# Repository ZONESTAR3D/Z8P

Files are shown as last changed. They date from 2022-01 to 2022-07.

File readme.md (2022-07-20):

# Z8P Documents

### Download Z8P documents
[**Download all the Z8P documents in one go**](https://downgit.github.io/#/home?url=https:%2F%2Fgithub.com%2FZONESTAR3D%2FZ9%2Ftree%2Fmain%2FZ8P)     

## 1. Installation and User Guide
- [**Z8PM3(4) Installation and quick user guide V1.pdf**](./1.%20Installation%20and%20User%20Guide/Z8PM3(4)%20Installation%20and%20quick%20user%20guide%20V1.pdf)  Installation and quick user guide.    
- [**Z8PM3(4)-Pro Installation and quick user guide V1.pdf**](./1.%20Installation%20and%20User%20Guide/Z8PM3(4)Pro%20Installation%20and%20quick%20user%20guide%20V1.pdf)  Installation and quick user guide.  
- [**LCD2864 Menu Description.pdf**](./1.%20Installation%20and%20User%20Guide/LCD12864%20Menu%20Description%20V6.pdf)  for Z8PM3(4), 128x64 LCD screen Menu instruction
- [**LCD-DWIN Menu Description.pdf**](./1.%20Installation%20and%20User%20Guide/LCD-DWIN%20MENU%20Description%20V1_2.pdf) for Z8PM3(4)Pro, 4.3" TFT-LCD screen MENU instruction of 
- [**Z8PM3(M4) Wiring Diagram.jpg**](./1.%20Installation%20and%20User%20Guide/Z8P_Wirig%20Diagram.jpg)  Wiring Diagram for Z8PM3(4)
- [**Z8PM3(M4)-Pro Wiring Diagram.jpg**](./1.%20Installation%20and%20User%20Guide/Z8P_Pro_Wirig%20Diagram.jpg)  Wiring Diagram for Z8PM3(4)-Pro  
- [**How to Load and Unload filament.pdf**](./1.%20Installation%20and%20User%20Guide/How%20to%20Load%20and%20Unload%20filament%20(LCD12864).pdf) Instrution for how to load and unload filament.  
- [**Operature guide for Mixing Color Printer.pdf**](./1.%20Installation%20and%20User%20Guide/Operature%20guide%20for%20Mixing%20Color%20Printer%20V1_2.pdf) Instrution for Operate the Mixing Color Extruder. 
- [**Bed auto leveling**](./1.%20Installation%20and%20User%20Guide/Bed%20Auto%20Leveling/) This directory has instructions on how to do the auto leveling and a leveling test gcode file. 
- [**Advanced Features**](./1.%20Installation%20and%20User%20Guide/Advanced%20Features/) Instrution for Advanced Features.  
## 2.Slicing
Please click this link to read the newest [**slicing guide**](https://github.com/ZONESTAR3D/Slicing-Guide).  
## 3. Test gcode
[Included some gcode files for testing.](./3.%20Test%20gcode/)
## 4. FAQ
[Included some TroubleShootings files.](./4.%20FAQ/)
## 5. Firmware   
- [**Firmware hex file**](https://github.com/ZONESTAR3D/Firmware/tree/master/Z8/Z8P)   
- [**Firmware sourc code**](https://github.com/ZONESTAR3D/source-code-for-3d-printer)
## 6. Video tutorial
### :movie_camera:[Installation Guide](https://youtu.be/YV3dSoo5NOM)  
### :movie_camera:[Product introduction](https://youtu.be/NqhwHJeaFhI)

## 7. Parts STL
Inlcuded the print parts stl fils for Z8P.

## How to downlod files from Github page
#### Step 1: Click this link [**https://downgit.github.io/**](https://downgit.github.io/) 
#### Step 2: Copy the Github file or direcotry link which you want to download.
#### Step 3: Click download button and wait a few seconds, it will start to download automatically. 
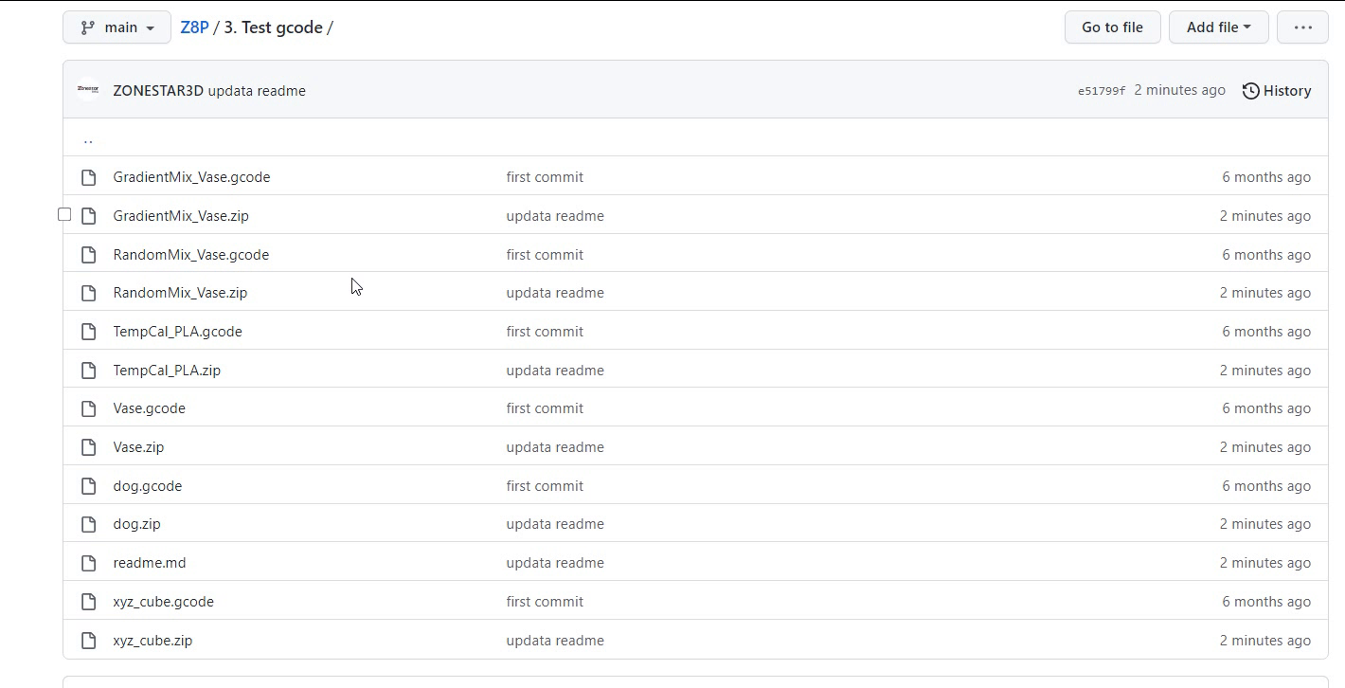
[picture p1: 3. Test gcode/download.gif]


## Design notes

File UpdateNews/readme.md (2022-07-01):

## Summary of Updates for ZONESTAR Z8P
### Updates in 2022-04-25
1. Release firmware V2.0.0 [View](https://github.com/ZONESTAR3D/Firmware/tree/master/Z8/Z8P/ZM3E4/released)
2. **E4 HOTEND** Update E4 hotend slicing settings [View](https://github.com/ZONESTAR3D/Upgrade-kit-guide/tree/main/HOTEND/E4%204-IN-1-OUT%20Non-Mixing%20Color%20Hotend/example)
3. **Slicer** Update PrusaSlcier prifiles for Z8(Z9)+E4 hotend and [View](https://github.com/ZONESTAR3D/Slicing-Guide/tree/master/PrusaSlicer)

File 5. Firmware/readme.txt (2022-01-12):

Firmware Upload Steps:
====
1. Download the zip file and unzip it
2. Copy firmware.bin to the root directory of Micro-SD card
3. Power off the printer and plug the Micro-SD card into socket on control board
4. Power on the printer, push the power button and wait about 30 seconds
5. Do the below step on LCD screen to initialize EEPROM after upload firmware:
MENU>>config>>Restore Defaults

Firmware
====
[**Firmware download link:**](https://github.com/ZONESTAR3D/Firmware/tree/master/Z8/Z8P)
[**Firmware Source code download link:**](https://github.com/ZONESTAR3D/source-code-for-3d-printer)

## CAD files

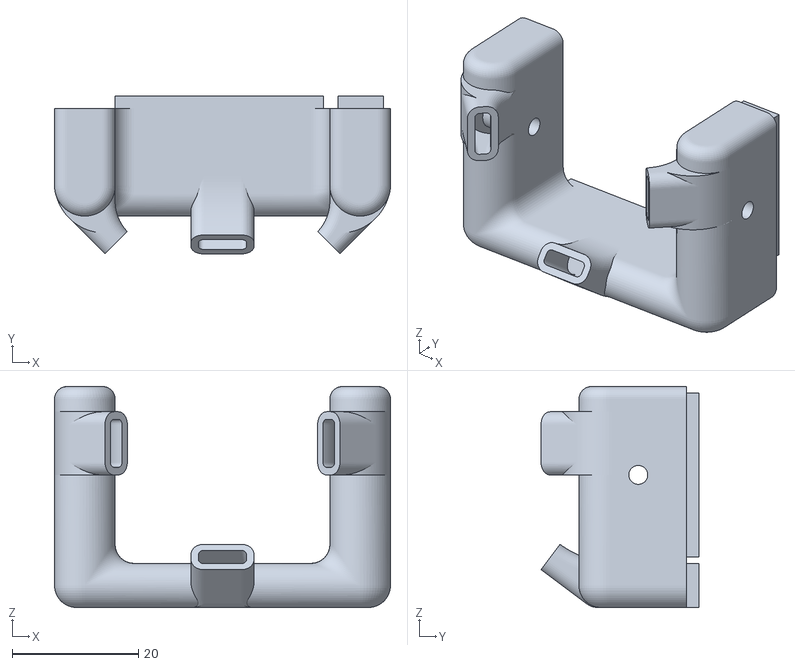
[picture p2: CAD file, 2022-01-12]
4. FAQ/fan_duck_m4_v3.stl
53.2 x 25.0 x 35.0

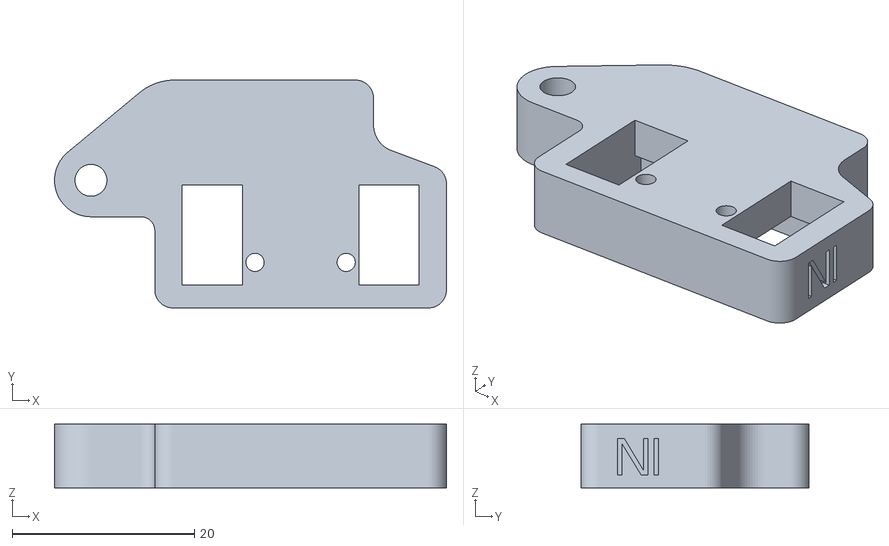
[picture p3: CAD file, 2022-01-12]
7. Parts STL/FRODV6-B.stl
43.0 x 25.0 x 7.00

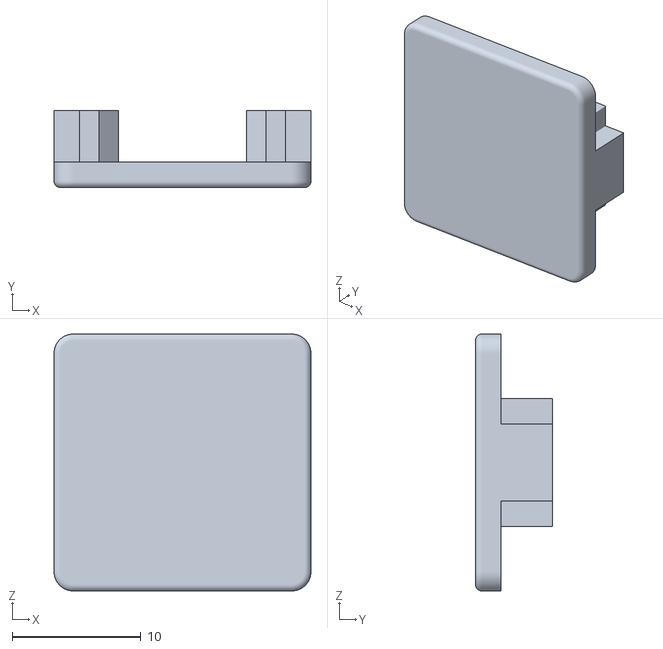
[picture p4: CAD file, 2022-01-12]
7. Parts STL/cap_af_20v.stl
20.0 x 6.00 x 20.0

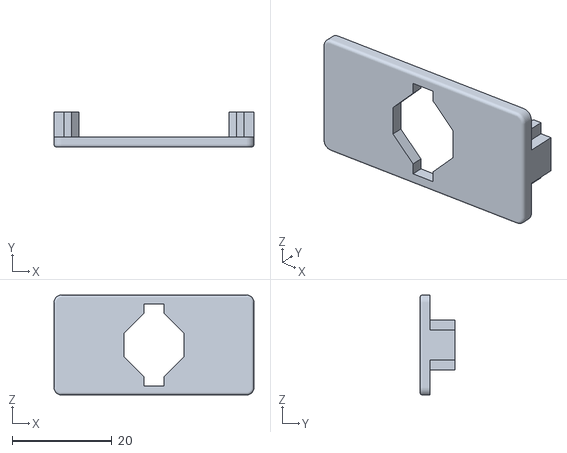
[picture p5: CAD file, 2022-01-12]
7. Parts STL/cap_af_40v.stl
40.0 x 7.00 x 20.0

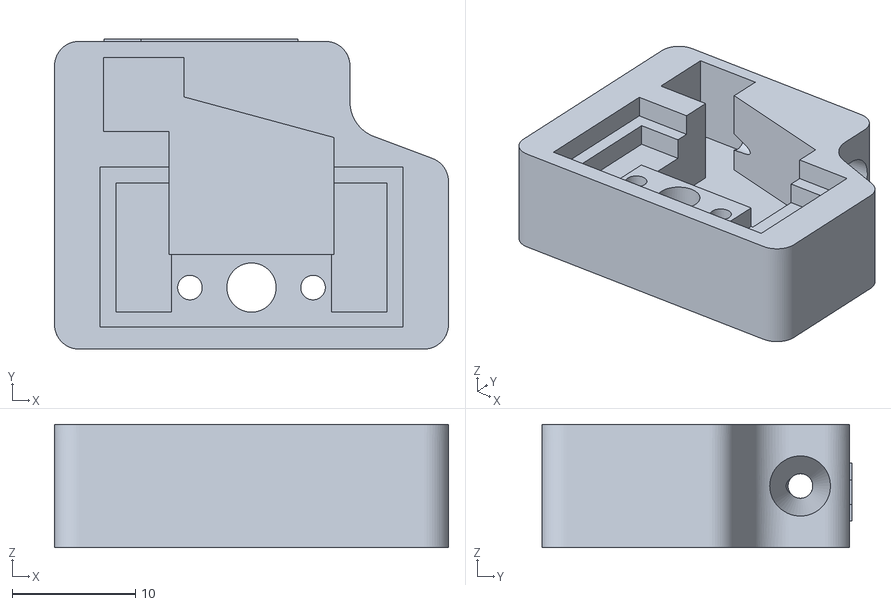
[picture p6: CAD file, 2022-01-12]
7. Parts STL/FRODV6-A.stl
32.0 x 25.2 x 10.0

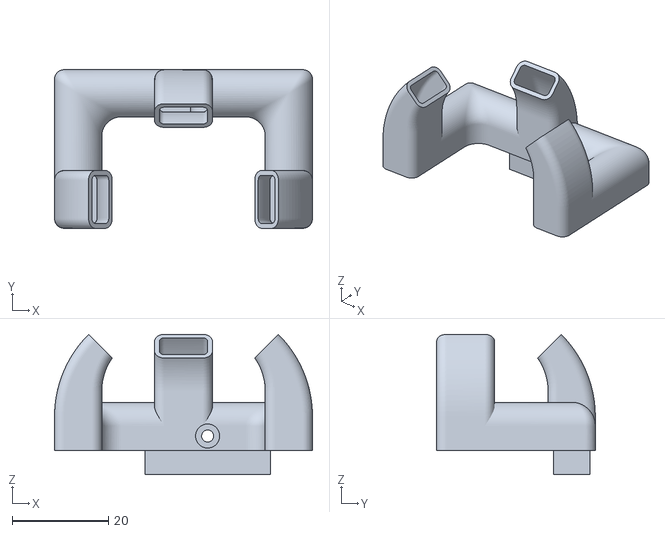
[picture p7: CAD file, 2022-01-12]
7. Parts STL/fanduck_m3_v4.stl
53.5 x 32.9 x 29.1

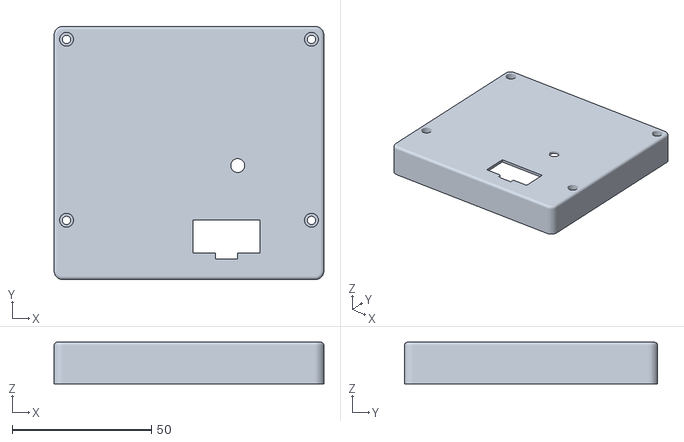
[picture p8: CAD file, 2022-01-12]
7. Parts STL/lcd12864_case_v2.stl
97.0 x 91.0 x 15.0

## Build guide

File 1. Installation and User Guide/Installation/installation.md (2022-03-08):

# Z8P Installation Guide
### :bangbang: ATTENTION :bangbang:
+ :warning: Please strictly follow the standard operation when installation.
+ :warning: Please put the printer away from the reach of kids.
+ :warning: Must be guided by adults when children are installed or used.
+ :zap: Take care when installation, to avoid electrical shock hazards.
+ :hotsprings: Hotend has high temperature even the printer stop working.
+ :hotsprings: Hotbed has high temperature even the printer stop working.
+ :dash: Keep well-ventilated condition! May produce toxic gases when printing.
+ :warning: Make sure the AC power select switch set correctly before power on.

## 1. Parts
### Parts list
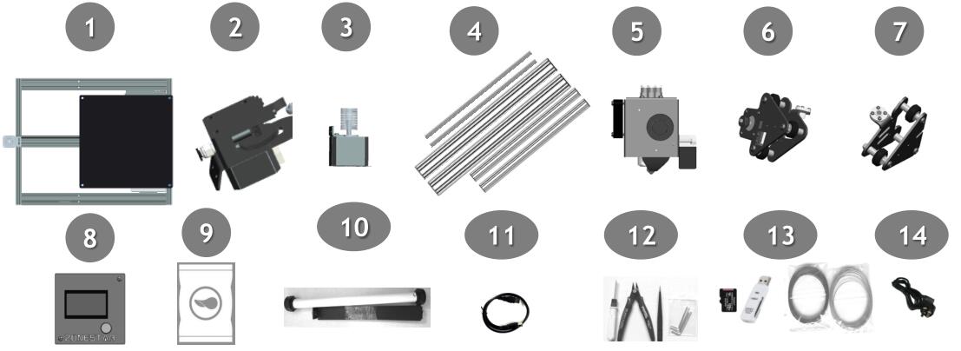
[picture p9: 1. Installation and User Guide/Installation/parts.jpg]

>
1. Base Module.    
2. Extruders Module (3 sets for M3 and 4 sets for M4).    
3. 2x Z-axis Motor Modules.  
4. Lead screw & Profiles.  
5. Print head with bracket (M3 or M4 hotend assembly).
6. Z carrier left.
7. Z carrier right.
8. Contol Panel (128x64 for Z8PM3(4) and TFT-LCD for Z8PM3(4)-Pro).  
9. Accessories bag, include: Scews, lead screws fix blocks, ENDSTOPs, Fittings,
PTFE Tubes, belt, cable tie, etc.  
10. Filament roll bracket.  
11. USB cable.  
12. Tools.  
13. SD card, Card Reader, Gift filament.  
14. AC power cord.  

### Parts description
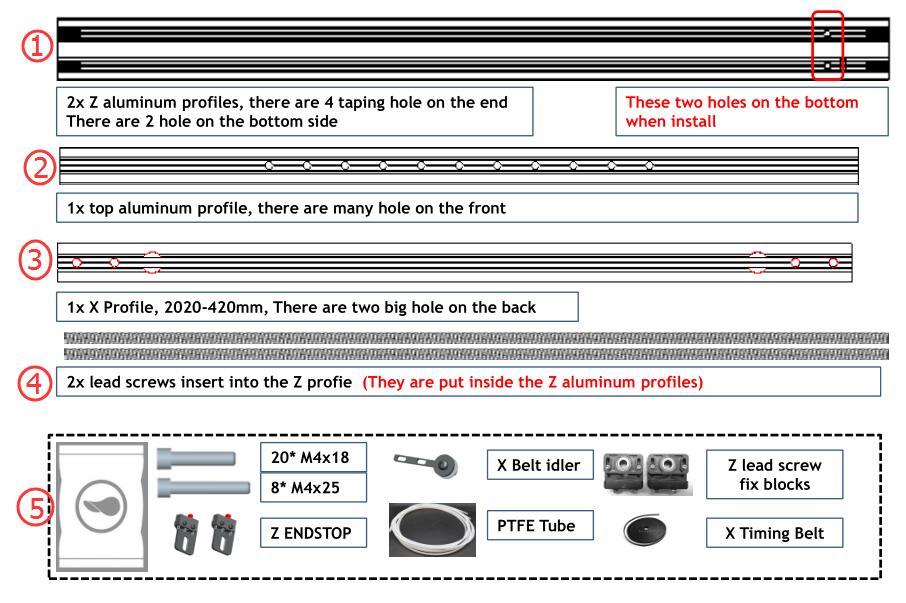
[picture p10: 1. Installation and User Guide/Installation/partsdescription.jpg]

>
1. Please note when install Z-profiles that side with two holes should be at the bottom.  
2. Pay attention to distinguish between X profile and TOP profile. The one with many holes is the TOP profile.  
3. Pay attention to the installation direction of the X profile. The side with two large holes faces back (touched the sheet metal of the Z carriers).  
4. The z-axis lead screw are placed in the z-axis profiles.  
5. Please check the packaging in the accessories bag.    

## 2. Installation
### 2-1: Install Z axis parts
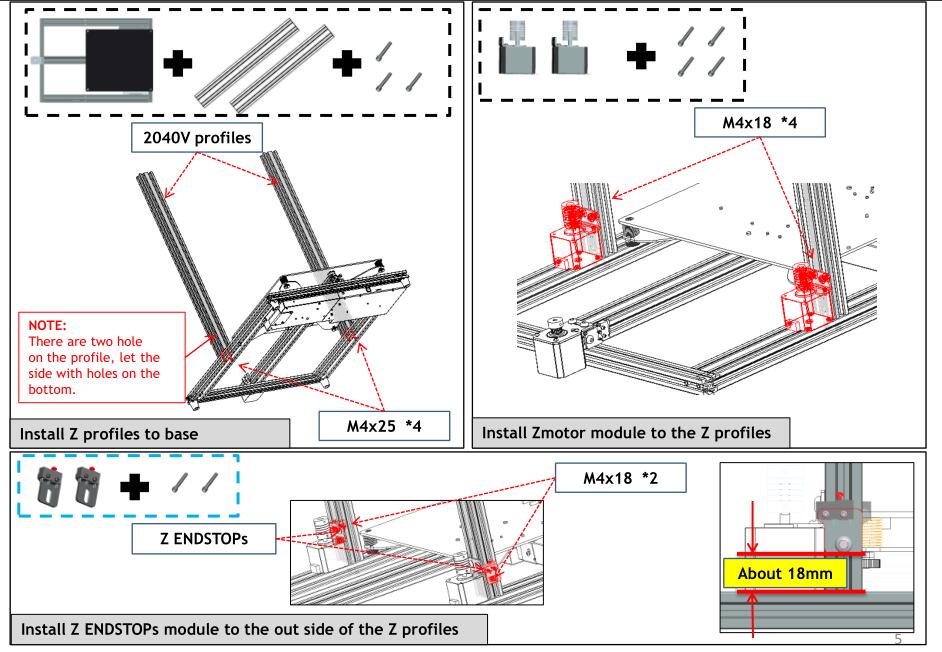
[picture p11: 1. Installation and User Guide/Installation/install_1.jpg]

> 
1. The side with 2 holes of the Z profiles is downward.
2. Alignment the side  of Z axis profile and the side of bottom profile of base module.  
3. Before installing the z-axis motor module on the profile, loosen the two screws fixing the motor a little.  
4. The Z ENDSTOPs should be mounted on the outside, and the install heigth is about about 18mm.

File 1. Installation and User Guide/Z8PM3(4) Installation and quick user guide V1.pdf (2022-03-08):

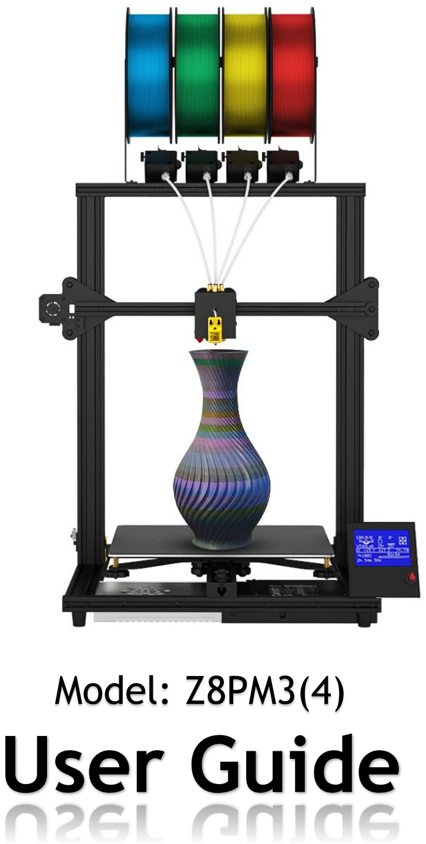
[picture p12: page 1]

# Model: Z8PM3(4)

# User Guide

Please put the printer away from the reach of kids.

Must be guided by adults when children are installed or used.

Take care when installation, to avoid electrical shock hazards.

## Please keep well-ventilated condition! May produce toxic gases when

printer working.

## Caution: Hot!

Hotend has high temperature even the printer stop working.

## Caution: Hot!

Hotbed has high temperature even the printer stop working.

Please strictly follow the standard operation when installation.

## Please make sure you have set the AC power select switch to the

correct position before power on.

## The newest documents download link:

## https://github.com/ZONESTAR3D/Z8P

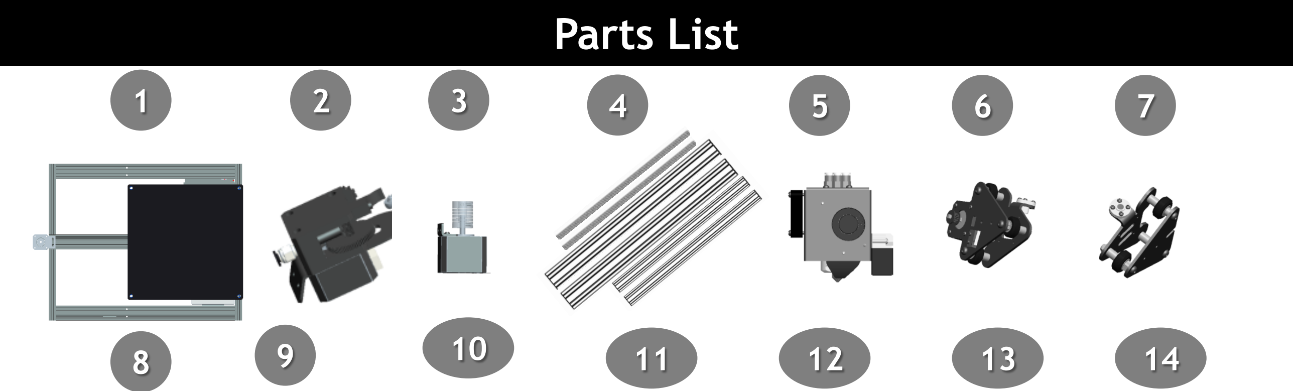
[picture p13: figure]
Parts List

No. | Name | Check | No. | Name | Check
1 | Base Module | □ | 8 | Contol Panel | □
2 | Extruders (3 sets for M3 and 4 sets for M4) | □ | 9 | Scews, lead screws fix blocks, ENDSTOPs, Fittings, PTFE Tubes, belt, cable tie, etc. | □
3 | Z-axis Motor Modules (2 sets) | □ | 10 | Filament Roll Bracket | □
4 | Lead screw & Profiles | □ | 11 | USB cable | □
5 | Print head with bracket M3 or M4 hotend | □ | 12 | Tools | □
6 | Z carrier left | □ | 13 | SD card, Card Reader, Gift filament | □
7 | Z carrier right | □ | 14 | Power cord | □

# Parts

2x Z aluminum profiles, there are 4 taping hole on the end There are 2 hole on the bottom side

These two holes on the bottom when install

1x top aluminum profile, there are many hole on the front

1x X Profile, 2020-420mm, There are two big hole on the back

2x lead screws insert into the Z profie (They are put inside the Z aluminum profiles)

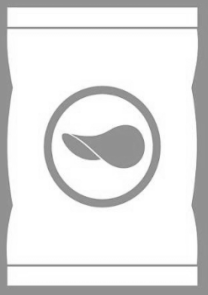
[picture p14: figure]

20* M4x18

8* M4x25

Z ENDSTOP

X Belt idler

PTFE Tube | X Timing Belt Z lead screw fix blocks

# Install Z axis Parts

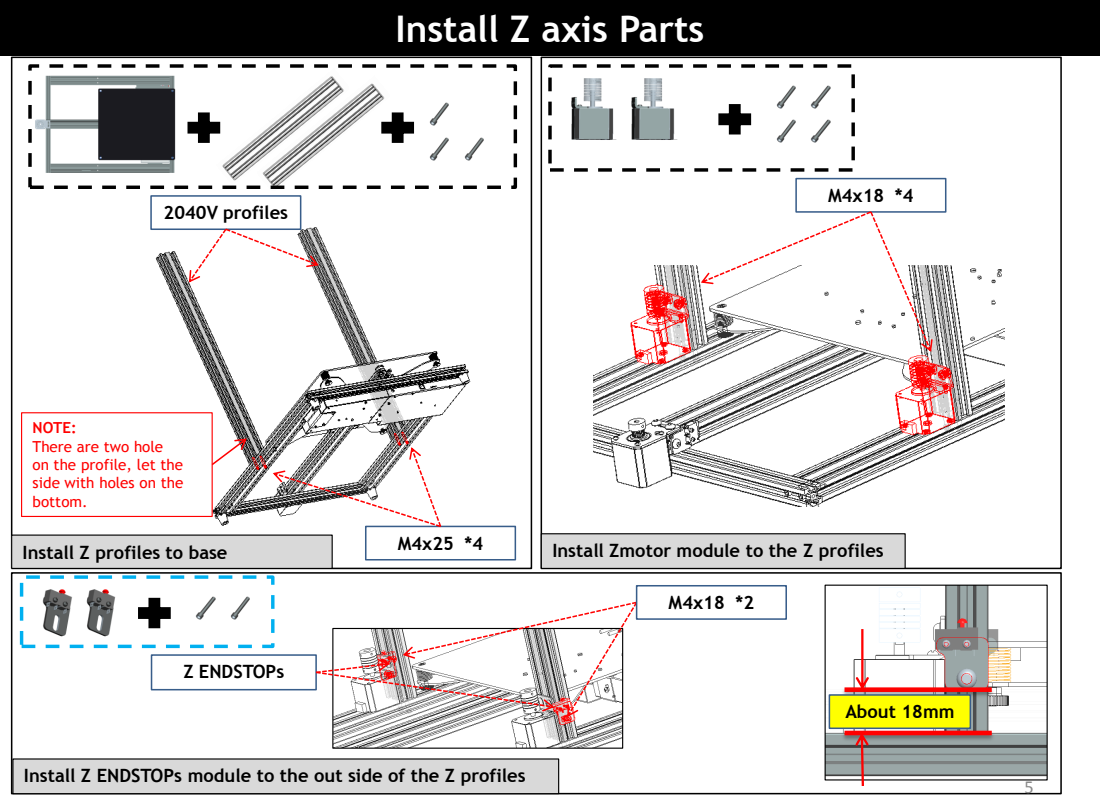
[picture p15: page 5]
2040V profiles; Z ENDSTOPs; About 18mm

NOTE:
There are two hole
on the profile, let the
side with holes on the
bottom.

Install Zmotor module to the Z profiles

Install Z profiles to base

Install Z ENDSTOPs module to the out side of the Z profiles

# Install Z axis Parts

Install Z Carrier | Install lead screws

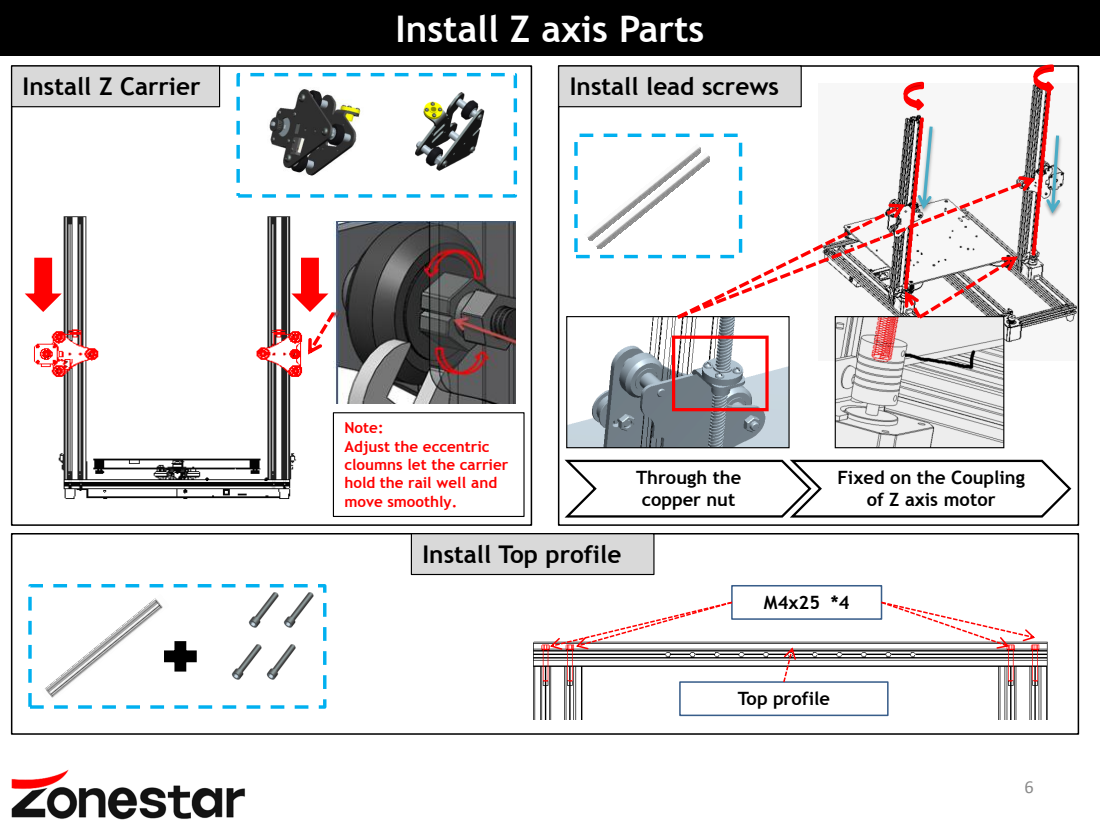
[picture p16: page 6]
Through the copper nut; Top profile

Note:
Adjust the eccentric
cloumns let the carrier
hold the rail well and
move smoothly.

Fixed on the Coupling
of Z axis motor

Install Top profile

# Install X axis Parts

## Install X belt idler and X profile

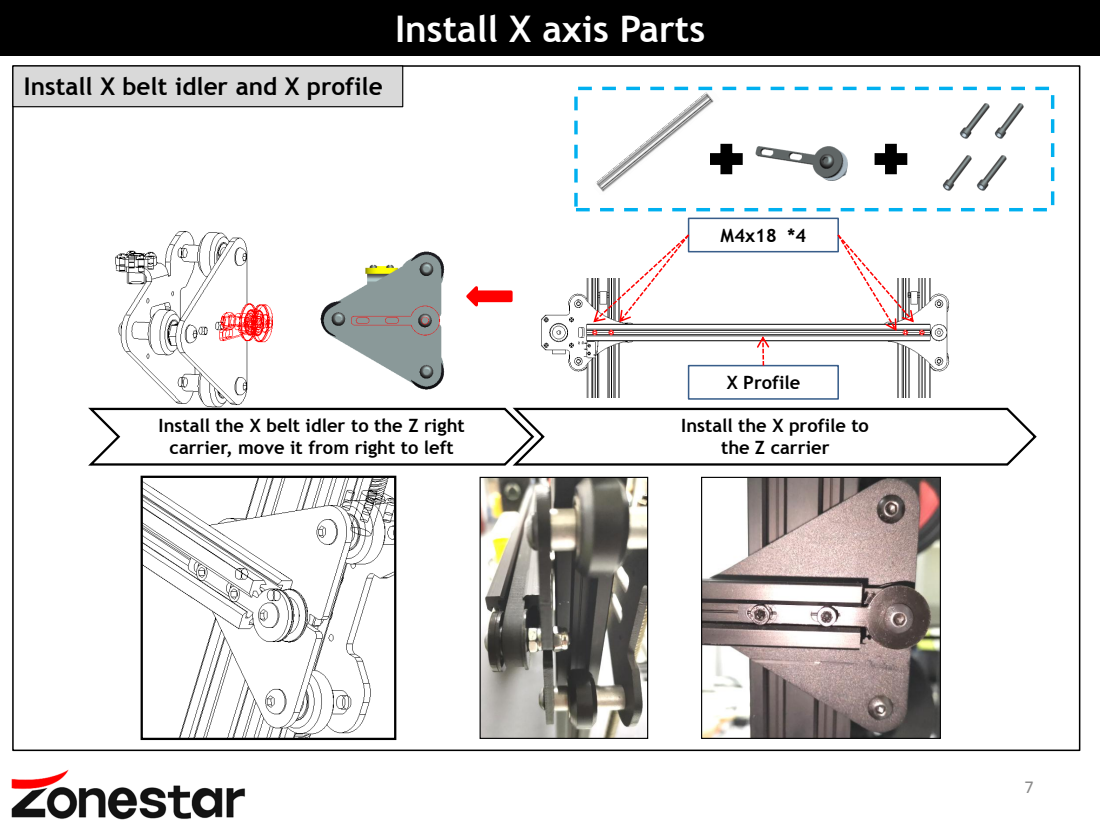
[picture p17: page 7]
X Profile

Install the X belt idler to the Z right
carrier, move it from right to left

Install the X profile to
the Z carrier

# Install X axis Parts

## Install X profile

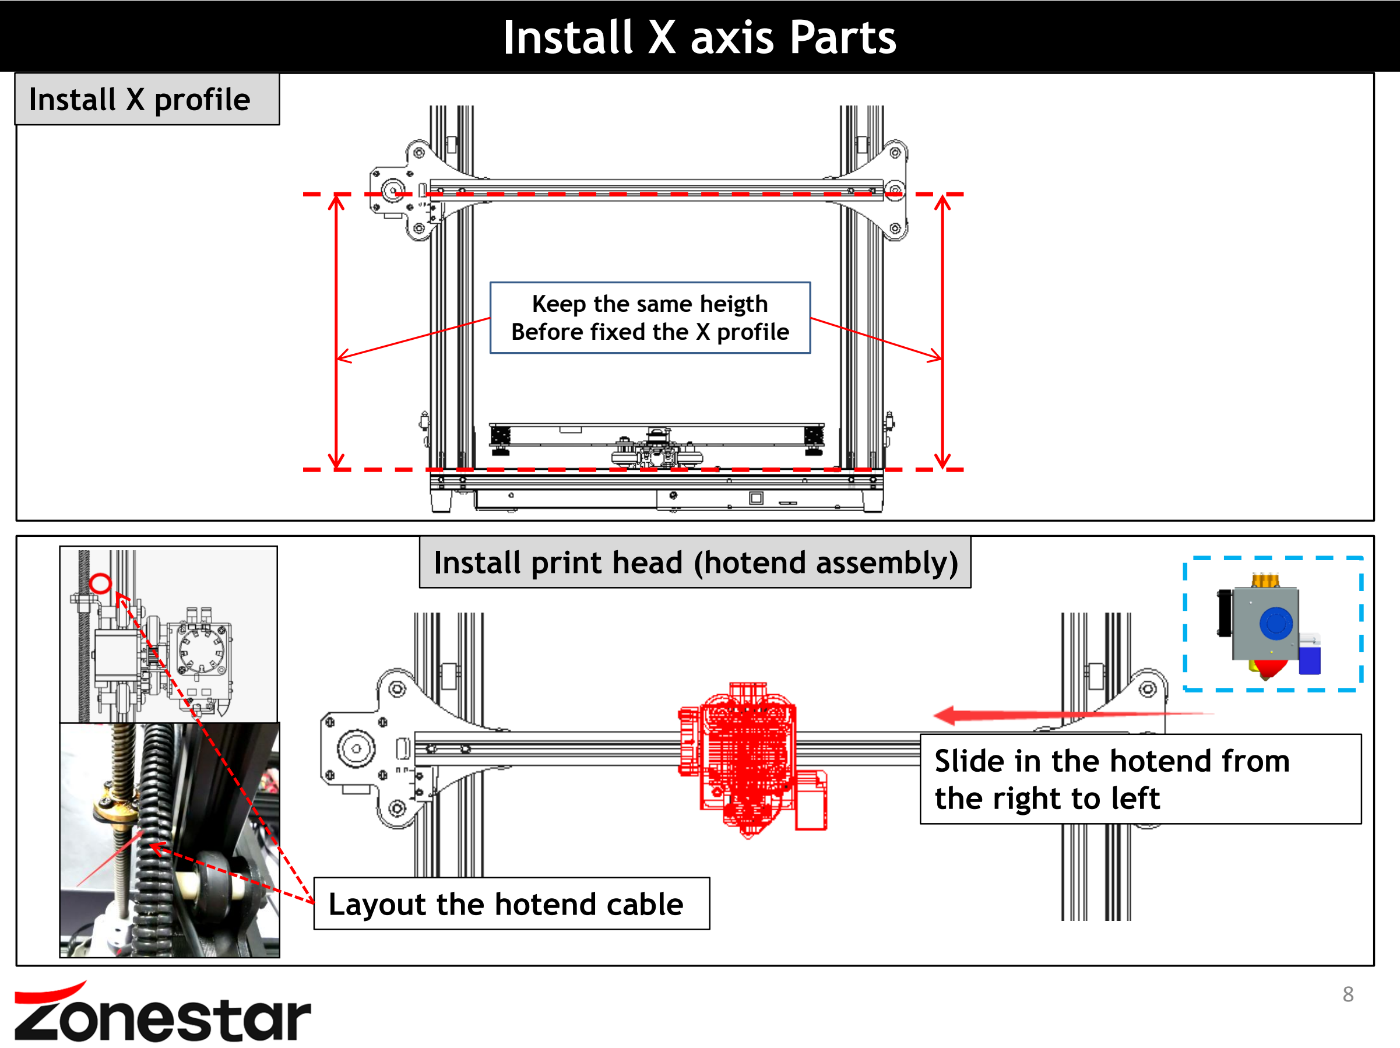
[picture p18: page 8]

## Slide in the hotend from the right to left

## Layout the hotend cable

Keep the same heigth
Before fixed the X profile

## Install print head (hotend assembly)

# Install X belt

## Install the X belt

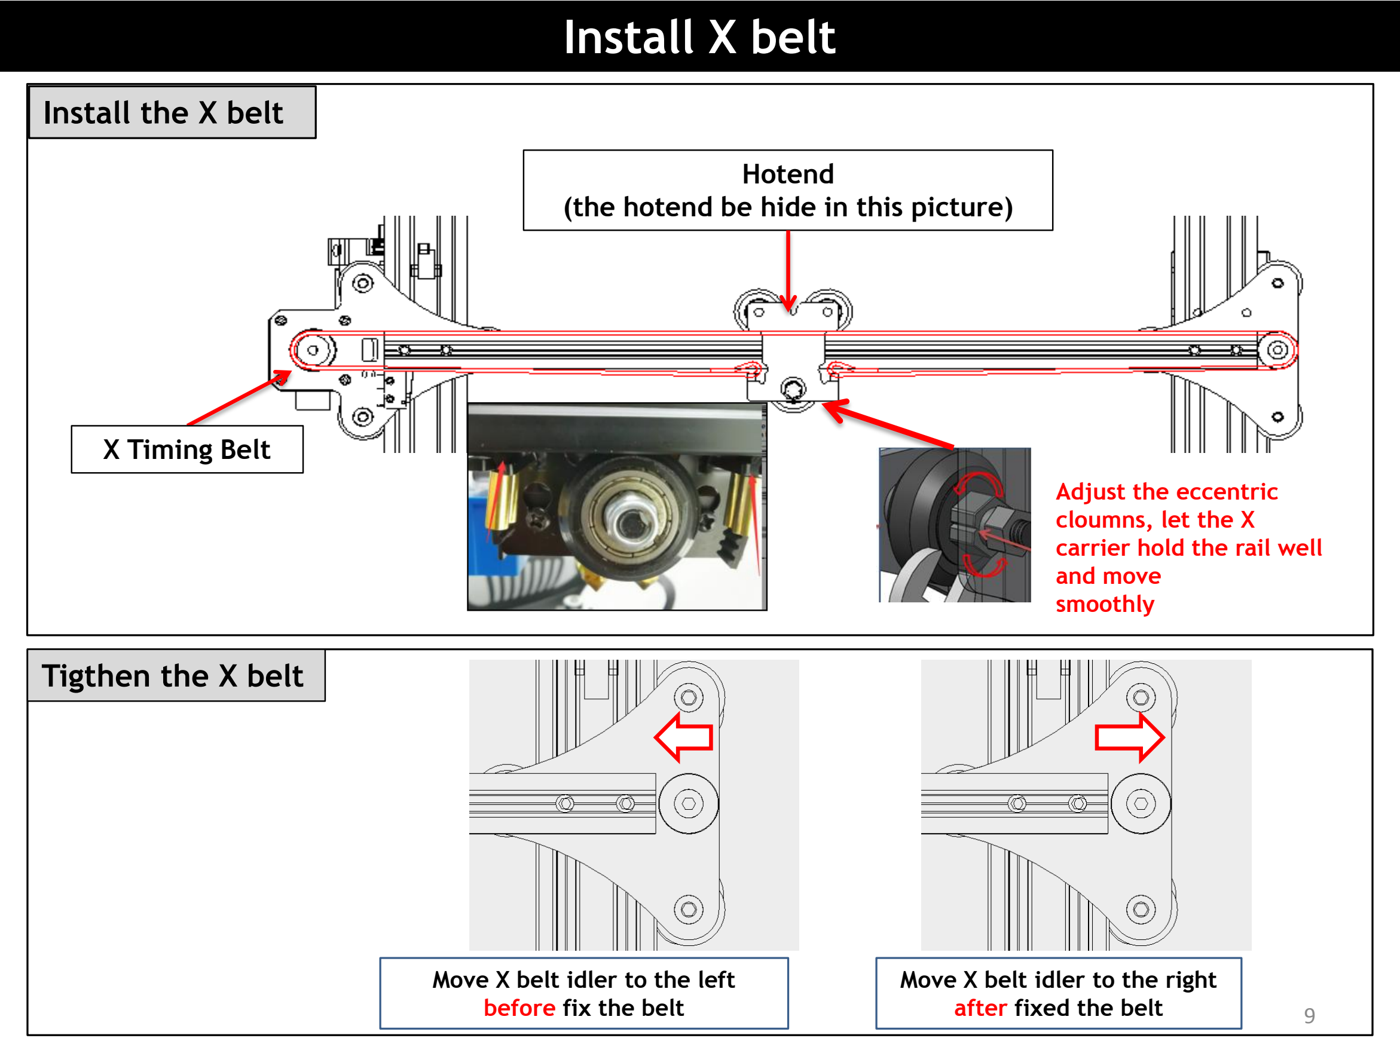
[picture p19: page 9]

Move X belt idler to the right
after fixed the belt | 9

Move X belt idler to the left before fix the belt

## Tigthen the X belt

X Timing Belt

Hotend
(the hotend be hide in this picture)

Adjust the eccentric
cloumns, let the X
carrier hold the rail well and move
smoothly

# Install the other parts

## x 3 o r 4

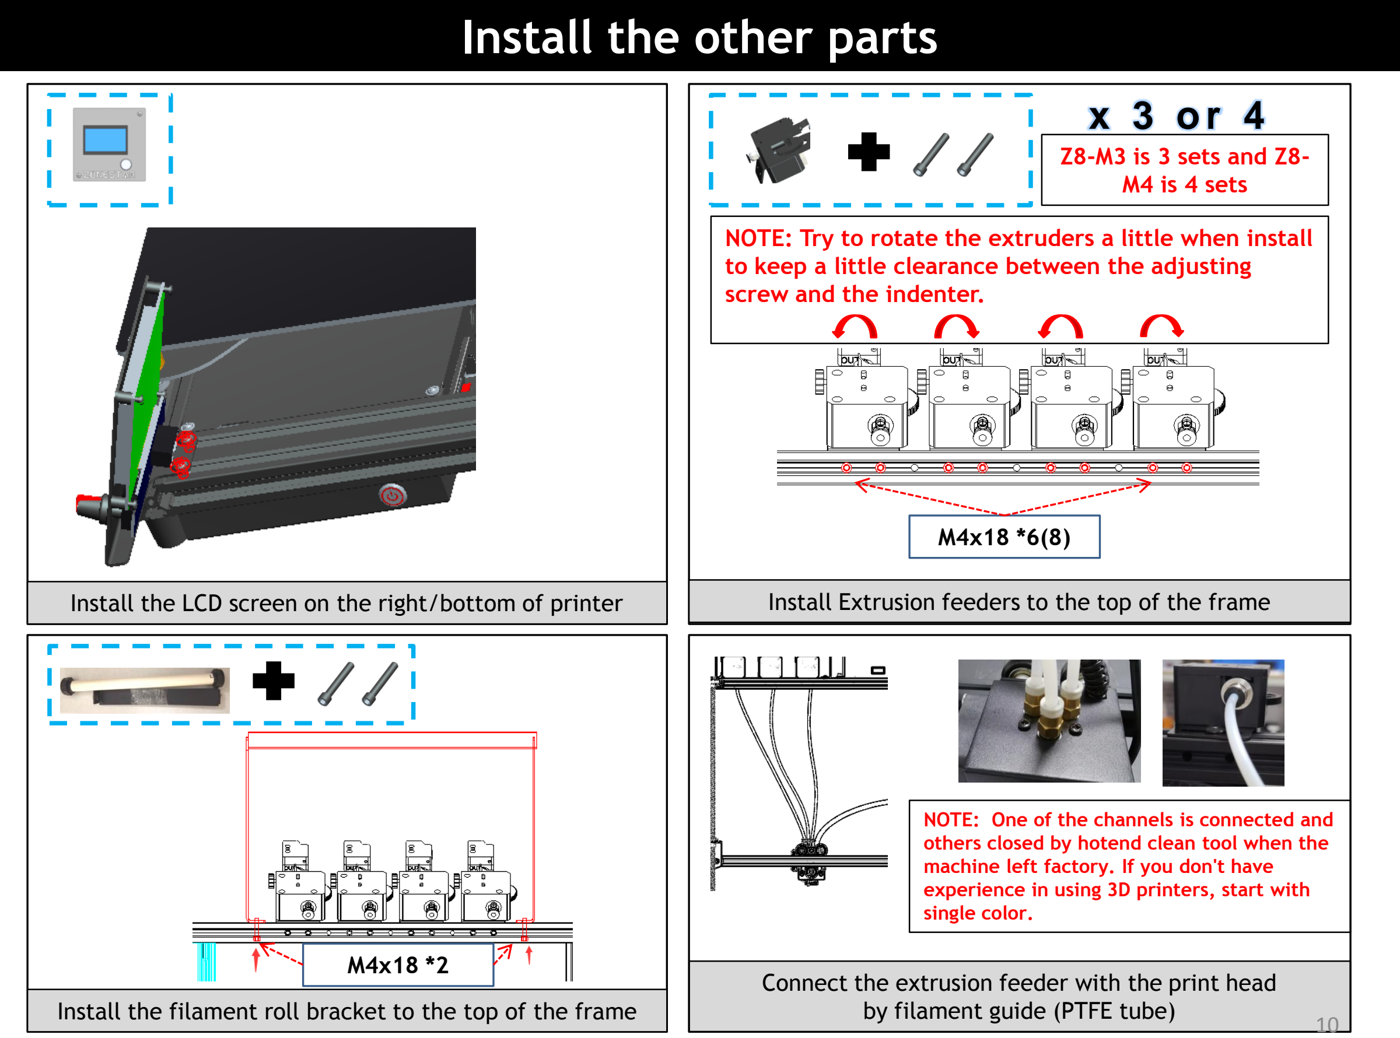
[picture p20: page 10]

Install the LCD screen on the right/bottom of printer

Z8-M3 is 3 sets and Z8-
M4 is 4 sets

Install the filament roll bracket to the top of the frame

Connect the extrusion feeder with the print head by filament guide (PTFE tube)

NOTE: One of the channels is connected and others closed by hotend clean tool when the machine left factory. If you don't have experience in using 3D printers, start with single color.

Install Extrusion feeders to the top of the frame

M4x18 *6(8)

NOTE: Try to rotate the extruders a little when install to keep a little clearance between the adjusting screw and the indenter.

M4x18 *2

Keep the lead screws parallel to the Z axis profiles as far as possible will help to obtain better printing quality, please debug them refer to the following steps: Step 1. Loosen all the screws a little that fixed the Z motors and T8 copper nut. Step 2. Synchronous Rotate the couplings to move up the X axis to 1/2 height of the printer. Step 3. Keep the lead screws parallel to the Z profiles, then tighten the screws that fixed the Z motor

| Loosen a little

and T8 copper nuts.
Step 4. Install the Z lead screws fix blocks on the top profile after done.

200mm

Put in

Fixed

Fixed

# Adjust height of Z ENDSTOPs

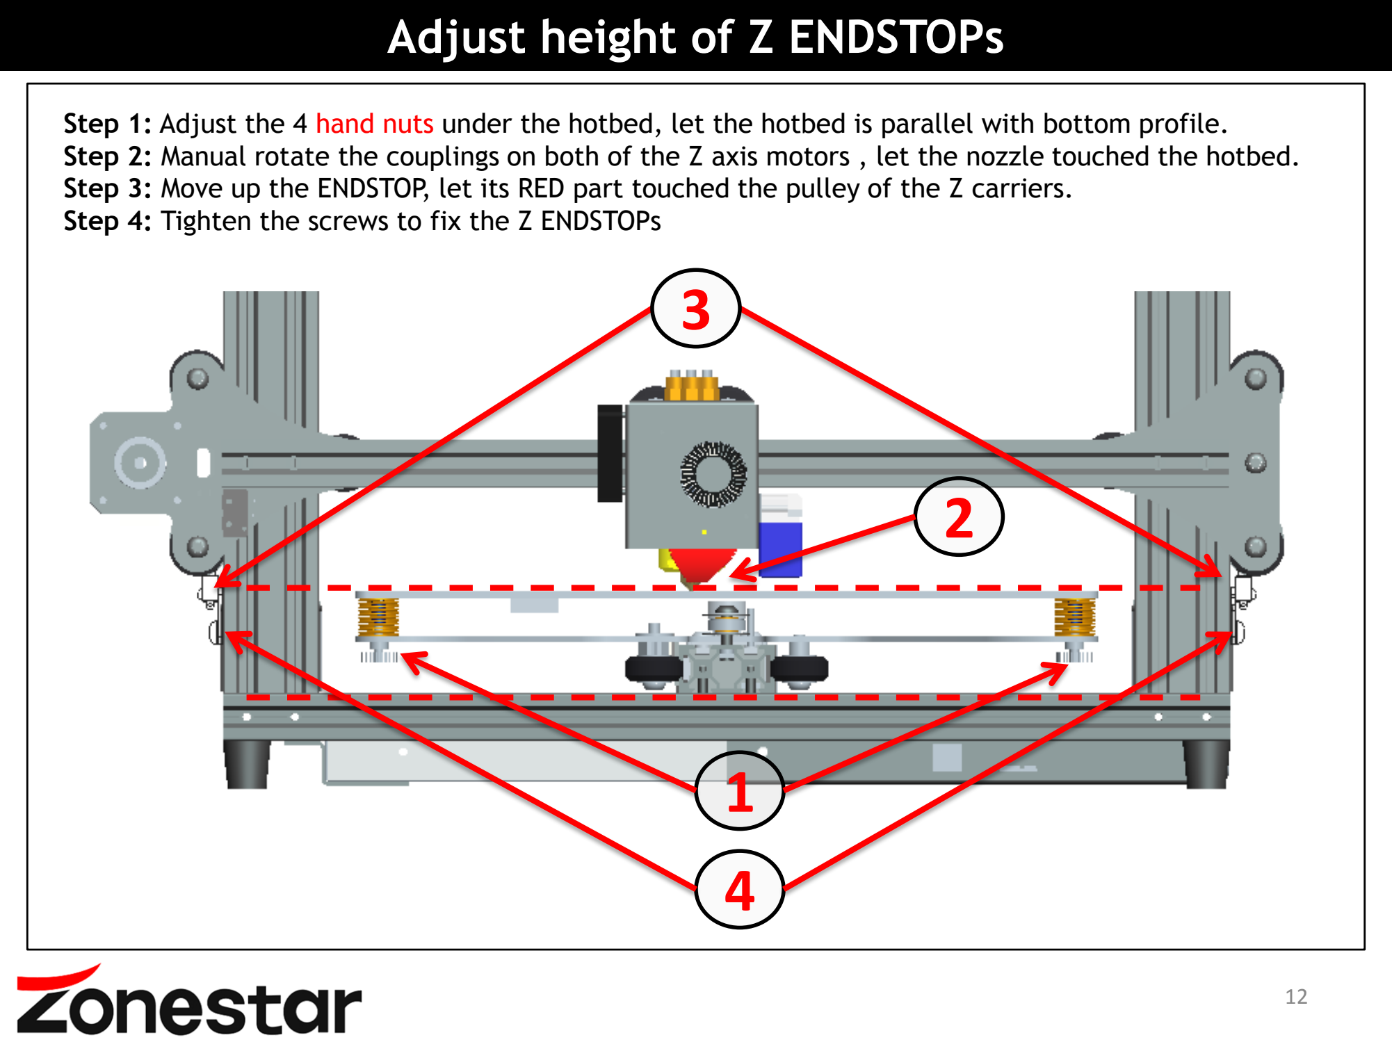
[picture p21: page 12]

Step 1: Adjust the 4 hand nuts under the hotbed, let the hotbed is parallel with bottom profile.
Step 2: Manual rotate the couplings on both of the Z axis motors , let the nozzle touched the hotbed.
Step 3: Move up the ENDSTOP, let its RED part touched the pulley of the Z carriers.
Step 4: Tighten the screws to fix the Z ENDSTOPs

1

2

4

3

## Take care when installation, to avoid electrical shock hazards!

## Double check the wiring! WRONG WIRING MAY DAMAGED THE ELECTRONIC DEVICE!

## Set the 110V/220V swicth (on the side of power supply) to correct position according to your city power voltage!

## Put the motor wire to the grooves of profile and cover them by

plastic profile cover, and using cable tie to wrap the free wires.

## Stop working immediately if the motor has abnormal vibration or noise,, otherwise the driver modules may be damaged!

## Make sure the hotend cooling fan is working when the nozzle

temperature is over 60 degree, otherwise check the wiring again.

## DC-IN, HOTBED has lager operating current, please make sure

these wires contact well with the terminal.

# About electronics parts

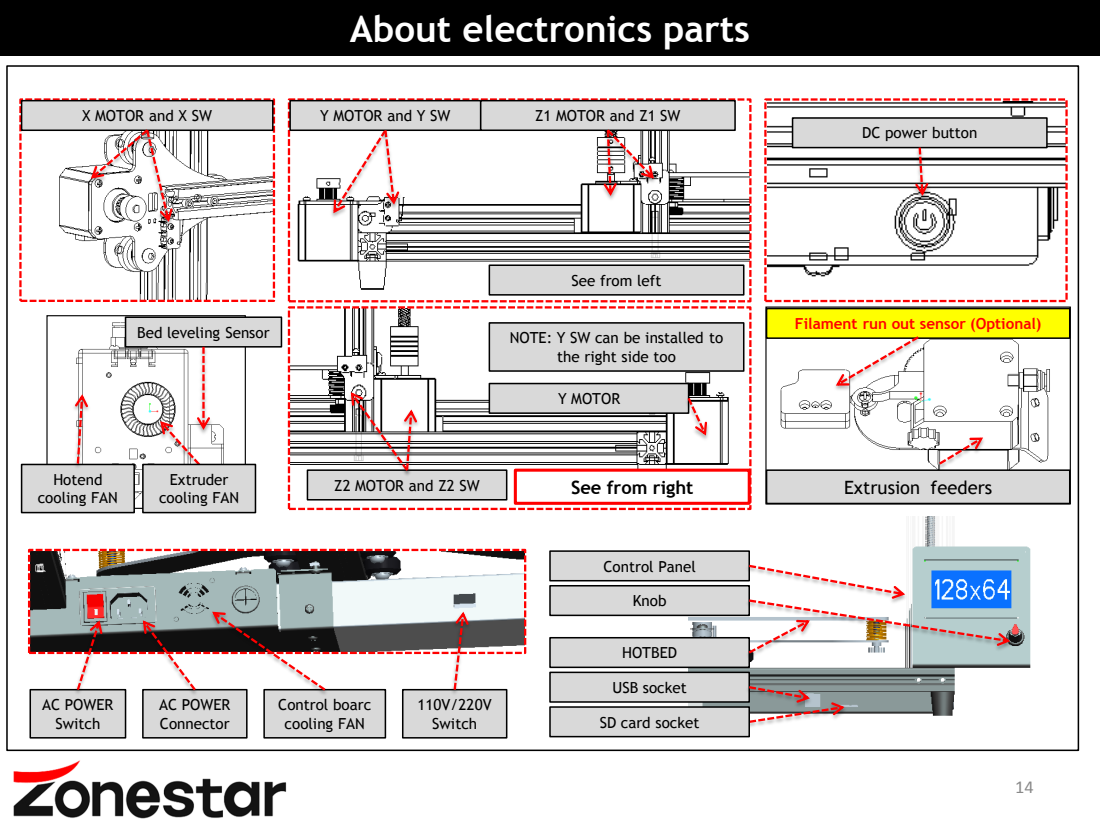
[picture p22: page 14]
X MOTOR and X SW; Y MOTOR and Y SW; Z1 MOTOR and Z1 SW; Extrusion feeders; Hotend cooling FAN; Y MOTOR; AC POWER Switch; AC POWER Connector; Control boarc cooling FAN; 110V/220V Switch; Control Panel; HOTBED; USB socket; Extruder cooling FAN; Knob

DC power button

See from left

Filament run out sensor (Optional)

Bed leveling Sensor

NOTE: Y SW can be installed to

the right side too

Z2 MOTOR and Z2 SW

See from right

SD card socket

# Wiring Block

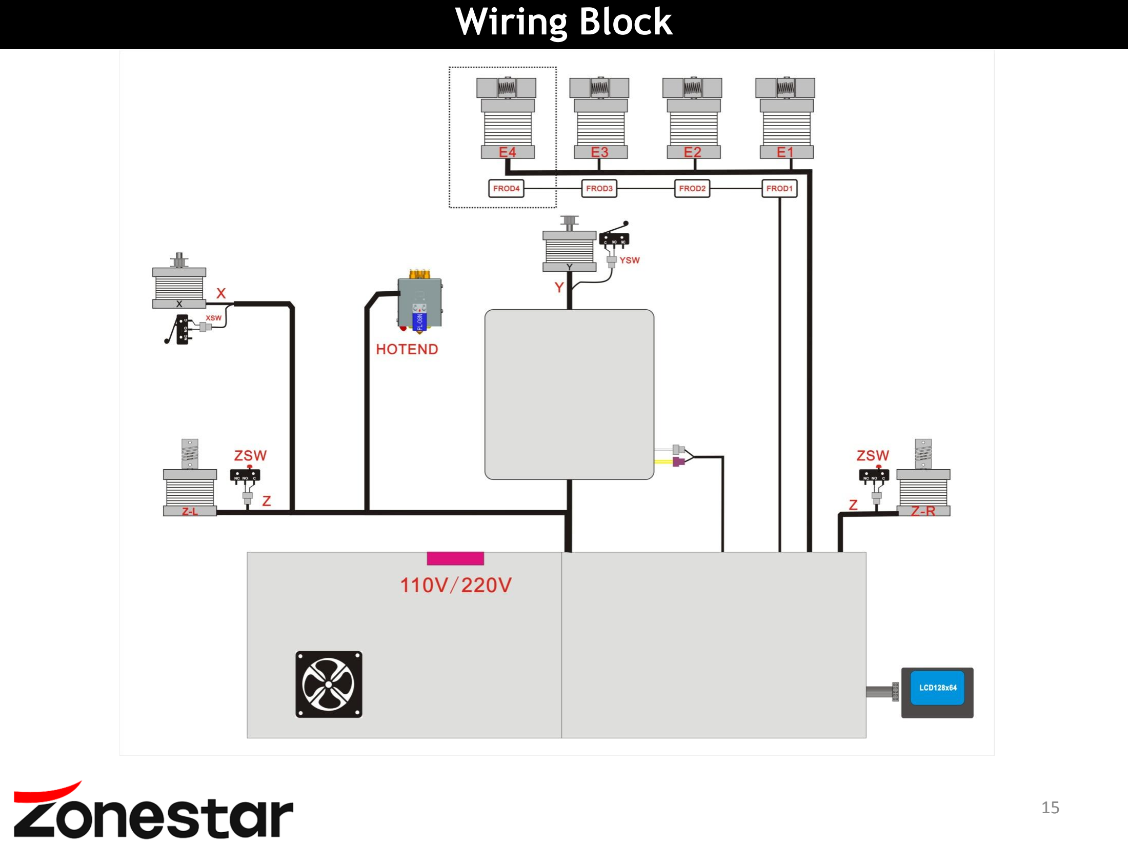
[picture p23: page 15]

# Layout the wires / cables

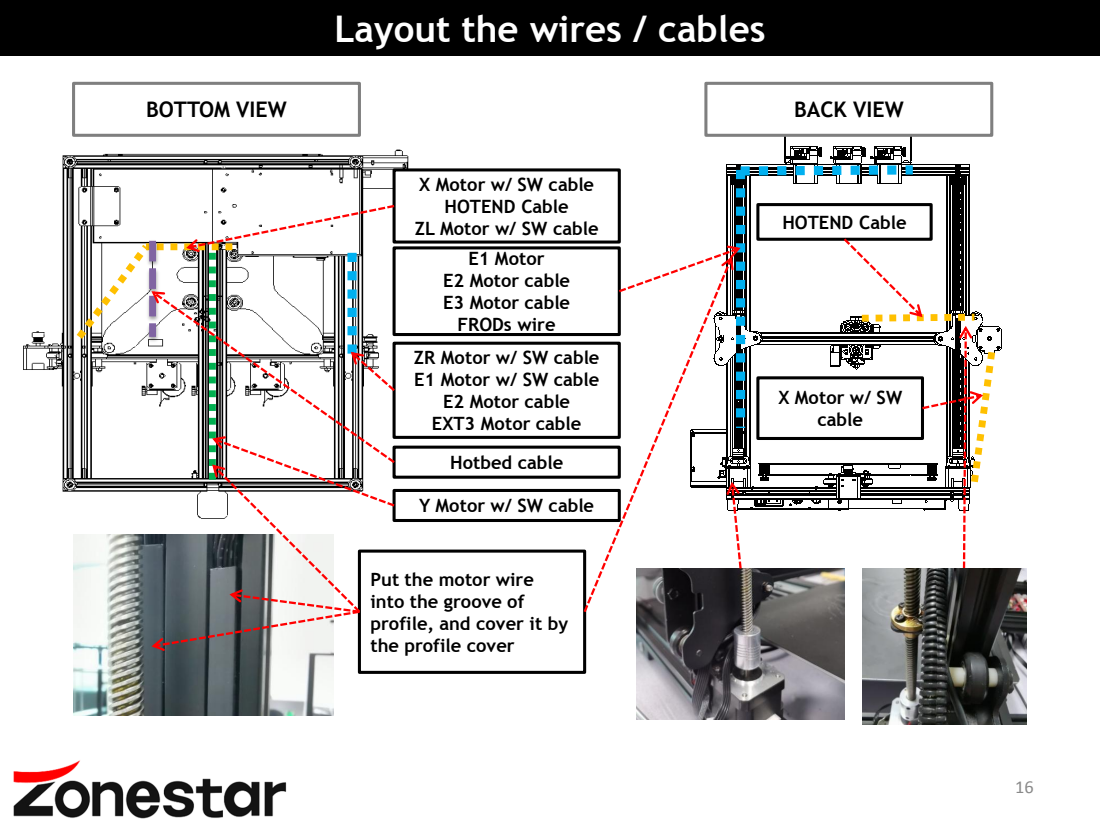
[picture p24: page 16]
Hotbed cable; BOTTOM VIEW; BACK VIEW; HOTEND Cable; X Motor w/ SW cable

X Motor w/ SW cable
HOTEND Cable
ZL Motor w/ SW cable

E1 Motor
E2 Motor cable
E3 Motor cable
FRODs wire
ZR Motor w/ SW cable
E1 Motor w/ SW cable
EXT3 Motor cable

Y Motor w/ SW cable

Put the motor wire
into the groove of
profile, and cover it by
the profile cover

Step 4: Manually move the hotend and hotbed to see if the movement is smooth, otherwise,

## adjust the eccentric nut until the motor moves smoothly. Refer to the installation

procedure.

## Step 3: Move the hotend and hotbed to their respective limit switch positions to check whether the contact is good and there is a clear sound. Otherwise, please check the limit

switch and reassemble it.

## Step 7: Manually rotate the z-axis screw rod to check whether the z-axis limit switch

contacts reliably.

Step 5: Check whether the X and Y-axis drive belt is firmly installed. If it is too loose, please try to tighten it.

## It is very important to check the machine before power on. It can eliminate the trouble brought by some hardware to ensure the smooth printing!

## Step 6: Check whether the screw rod is assembled in place and whether the screw is tightened

Step 1:Please check if the X&Y axis timing pulley are fixed on the shaft of motor, and the couplings are fixed on the shaft of the Z motors.
Step 2:Please check if the lead screws have been fixed on the shaft of coulping.

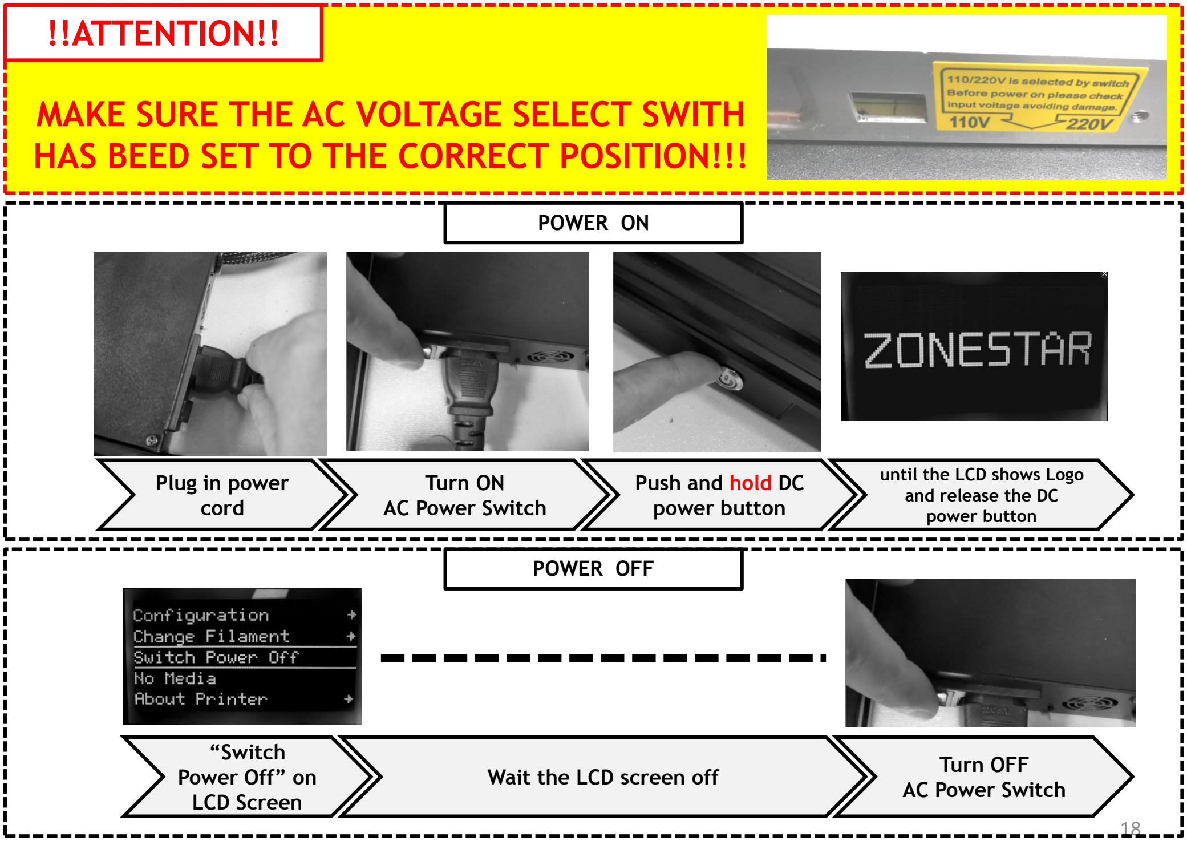
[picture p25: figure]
Wait the LCD screen off; POWER OFF; “Switch Power Off” on LCD Screen; Turn OFF AC Power Switch; Plug in power cord; Turn ON AC Power Switch; Push and hold DC power button; until the LCD shows Logo and release the DC power button; POWER ON; !!ATTENTION!!; MAKE SURE THE AC VOLTAGE SELECT SWITH HAS BEED SET TO THE CORRECT POSITION!!!

## Knob operation: <Clockwise rotation>: Next Item / Value +. <Counterclockwise rotation>:

Previous Item / Value -. <Push>: Enter / Execute.

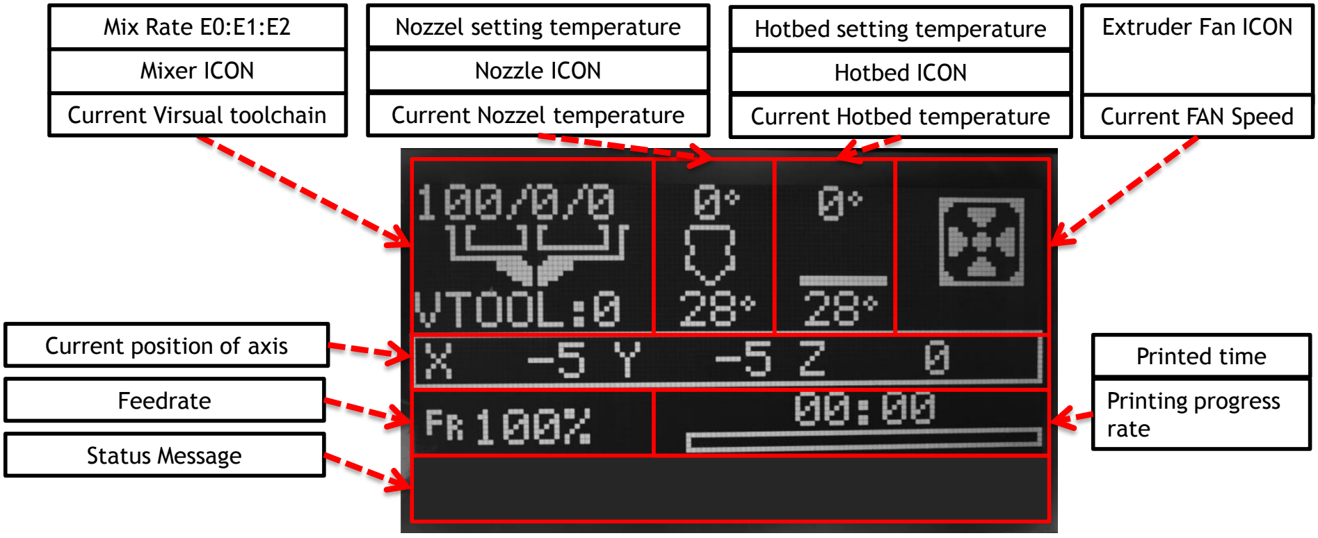
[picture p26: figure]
Status Message; Printed time; Printing progress rate; Extruder Fan ICON; Current position of axis; Feedrate; Current Virsual toolchain; Mix Rate E0:E1:E2; Mixer ICON; Nozzel setting temperature; Nozzle ICON; Current Nozzel temperature; Hotbed setting temperature; Hotbed ICON; Current Hotbed temperature; Current FAN Speed

For details on the LCD menu, please refer to "LCD12864 Menu Description".

VTOOL: In singel color or general multicolor printer, each extrude motor corresponds to one nozzle, then one extrude + one

nozzle constitutes one tool chain; In mixing color extruder, multiple extrude motors correspond to one nozzle. By setting rotation

ratios of extrude motors can form multiple VTOOL(virtual tool chains). About details, please refer to “Operature guide for

Mixing Color Printer”.

Feedrate: Rotate the knob to set print speed when printing from SD card.

Clean nozzle: make sure there aren't any filament at the end of nozzle, if not, remove it by a diagonal pliers.

1

2

3

Choose “Motion>> Auto Home”>>, wait the hotend go to the orig position.

Watch the nozzle and make sure the nozzle is higher than the bed, otherwise tighten the hand nuts under the bed to pull down the hotbed or loosen these nuts to move up the bed.

4

Choose “Motion>> Level Corners”>>, the nozzle will go to the corners, adjust the hand nuts under the hotbed, let the nozzle almost touch the hotbed. In order to get a properly distance, you can put a A4 paper on the hotbed, and when the distanse between the nozzle and hotbed can only insert a paper, it will be perfect.
Choose “next corner”, and adjust again. Repeat this step again and again, until all of the four corner at the same height. 5

## Congratulations! Now you have finished installation and check, you can start to print

your first works. Before printing, you need to level the hotbed first.

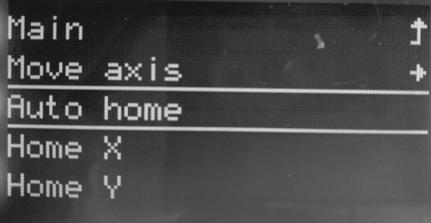
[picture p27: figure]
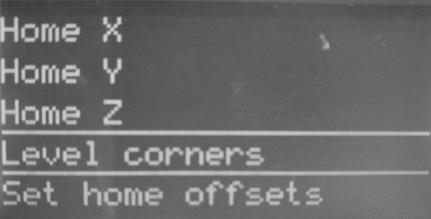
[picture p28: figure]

Preheat nozzle: Temperature>> Nozzle, set it to about 180 degree (for PLA) or 220 degree(for ABS and PETG filament), then nozzle will be heated. Waiting nozzle temperature reached to setting.

1

2

Press the handle on the extrude feeder and insert filament, until the filament enter to the hotend.

Choose “Motion>> Move axis>>Extruder>>Move 1mm>>extruder: ****mm”, then Clockwise rotate the knob slowly, until you can see the filament is flowed from the nozzle. 3

## NOTE: We strongly recommend that you start with single color. When the product leaves the factory, we have closed some channels with hotend cleaning tools. You can use

that unclosed channel to print your first work.

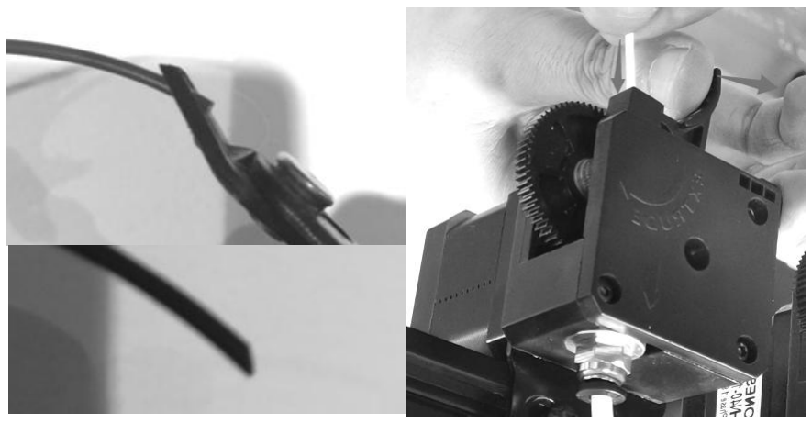
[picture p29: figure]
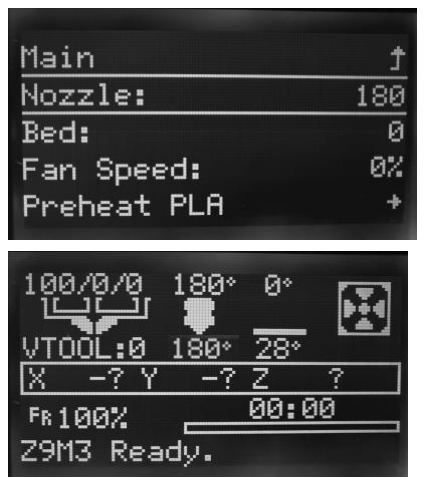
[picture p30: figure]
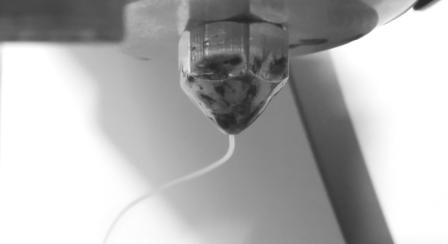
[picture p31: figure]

# Print a test 3D object (Print from SD card)

2

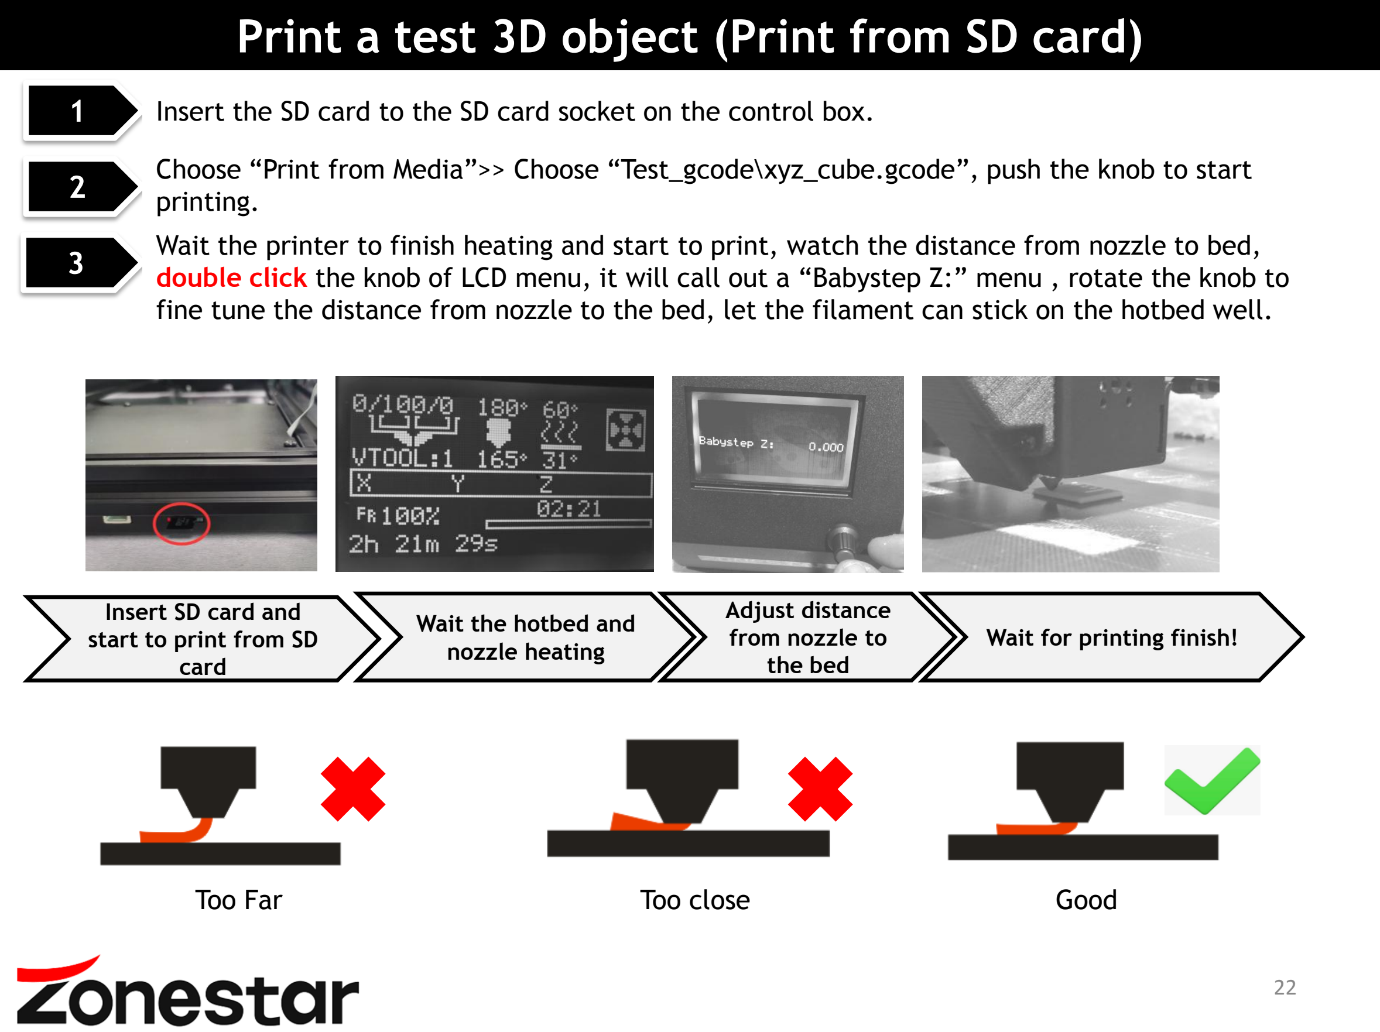
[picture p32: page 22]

1 Insert the SD card to the SD card socket on the control box.

Choose “Print from Media”>> Choose “Test_gcode\xyz_cube.gcode”, push the knob to start printing.

3

Wait the printer to finish heating and start to print, watch the distance from nozzle to bed, double click the knob of LCD menu, it will call out a “Babystep Z:” menu , rotate the knob to fine tune the distance from nozzle to the bed, let the filament can stick on the hotbed well.

Insert SD card and
start to print from SD
card

Wait the hotbed and
nozzle heating | Wait for printing finish!

Adjust distance
from nozzle to
the bed
Too Far | Too close | Good

# Slicing

## About slicing

Slicing a 3D drawing translates the 3D drawing into a language that a 3D printer can understand and print. The slicing software is a computer software used in the majority of 3D printing processes for the conversion of a 3D object model to specific instructions for the printer. In particular, the conversion from a model in STL(Obj, Amf) format to printer commands in g-code format. This machine can use a variety of slicing software to complete slicing. We will now introduce the most commonly used slicing software: Cura.
NOTE: 1. Slicing software is not a part of this machine. 2. You can download Cura for free from the internet.

## Install slicing software and step up the printer

In order to run the slicing software, you need a PC or laptabe, installed windows/linux/Macos.
Step 1: Download and install Cura to your PC, please search “ultimaker cura” from google.
Step 2: Copy “cura resources.zip” from the SD card and unzip it to your PC.
Step 3: Copy “resources” file to the same directory in cura which you installed.
Step 4: Run cura software, and follow the below steps to choose the printer.

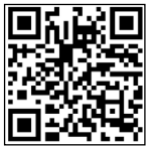
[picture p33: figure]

Download
Cura

Download
Slicing Guide
Load stl files | Setup settings

Slicing and
preview

Store to SD
card

## NOTE: For description of slicing, please refer to the documents in the

directory of “slicing”.

## Slicing process

## You can print something to upgrade your printer, we have made some printed part

and store the stl file to the SD card, you can feel free to slicing it and print it out, and then install them to your kit to make the printer better.

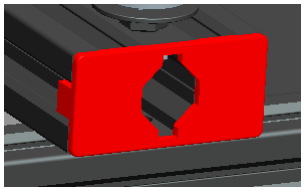
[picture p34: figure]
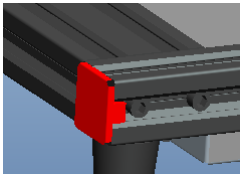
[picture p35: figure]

cap_af_20v.stl | cap_af_40v.stl

## lcd12864_case_v2.stl

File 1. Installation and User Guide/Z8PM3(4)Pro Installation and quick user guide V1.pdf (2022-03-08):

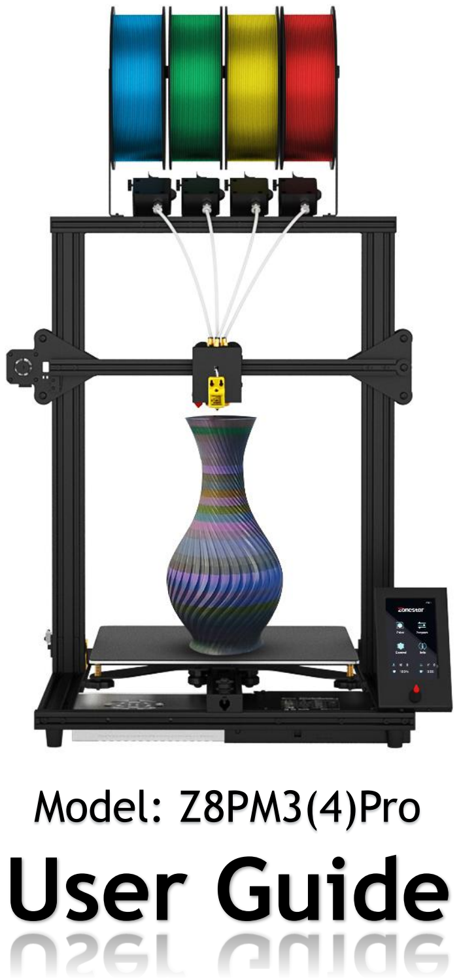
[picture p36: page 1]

# Model: Z8PM3(4)Pro

# User Guide

Please put the printer away from the reach of kids.

Must be guided by adults when children are installed or used.

Take care when installation, to avoid electrical shock hazards.

## Please keep well-ventilated condition! May produce toxic gases when

printer working.

## Caution: Hot!

Hotend has high temperature even the printer stop working.

## Caution: Hot!

Hotbed has high temperature even the printer stop working.

Please strictly follow the standard operation when installation.

## Please make sure you have set the AC power select switch to the

correct position before power on.

## The newest documents download link:

## https://github.com/ZONESTAR3D/Z8P

2

Parts List

No. | Name | Check | No. | Name | Check
1 | Base Module | □ | 8 | Contol Panel | □
2 | Extruders (3 sets for M3 and 4 sets for M4) | □ | 9 | Scews, lead screws fix blocks, ENDSTOPs, Fittings, PTFE Tubes, belt, cable tie, etc. | □
3 | Z-axis Motor Modules (2 sets) | □ | 10 | Filament Roll Bracket | □
4 | Lead screw & Profiles | □ | 11 | USB cable | □
5 | Print head with bracket M3 or M4 hotend | □ | 12 | Tools | □
6 | Z carrier left | □ | 13 | SD card, Card Reader, Gift filament | □
7 | Z carrier right | □ | 14 | Power cord | □

3

# Parts

2x Z aluminum profiles, there are 4 taping hole on the end There are 2 hole on the bottom side

These two holes on the bottom when install

1x top aluminum profile, there are many hole on the front

1x X Profile, 2020-420mm, There are two big hole on the back

2x lead screws insert into the Z profie (They are put inside the Z aluminum profiles)


20* M4x18

8* M4x25

Z ENDSTOP

X Belt idler

PTFE Tube | X Timing Belt Z lead screw fix blocks

4

# Install Z axis Parts

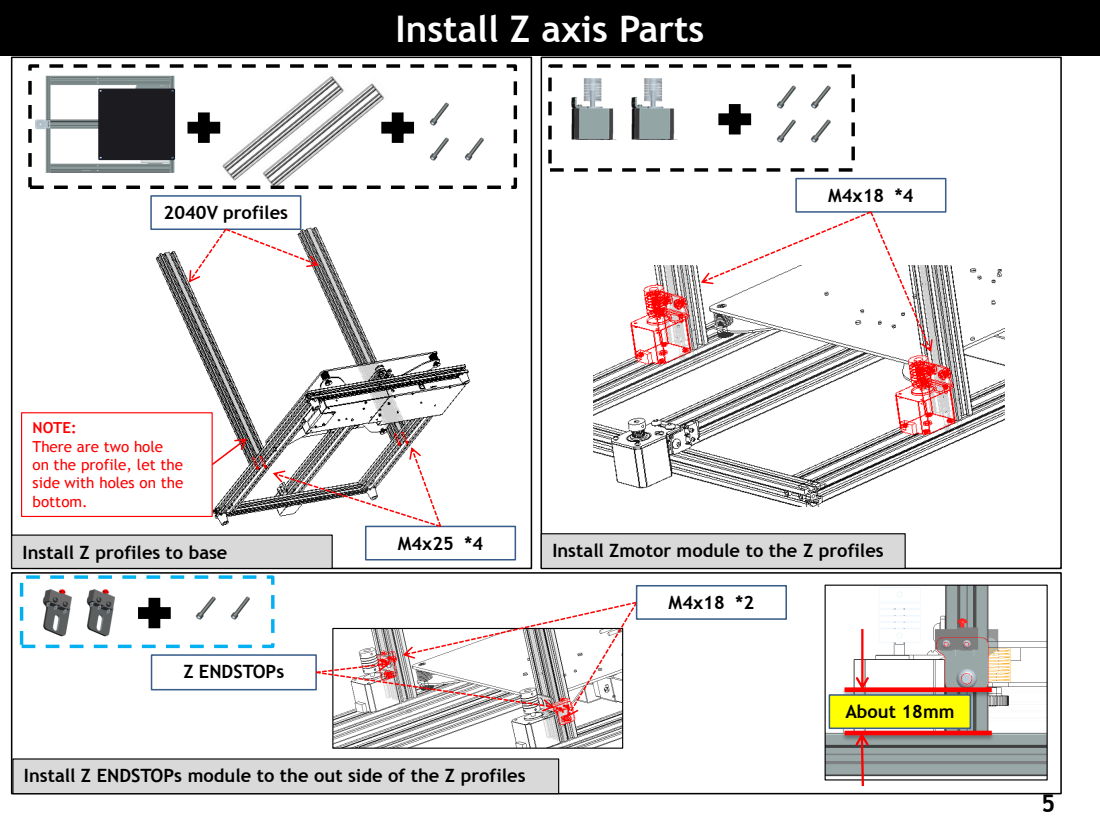
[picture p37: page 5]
2040V profiles; Z ENDSTOPs; About 18mm

NOTE:
There are two hole
on the profile, let the
side with holes on the
bottom.

Install Zmotor module to the Z profiles

Install Z profiles to base

Install Z ENDSTOPs module to the out side of the Z profiles

# Install Z axis Parts

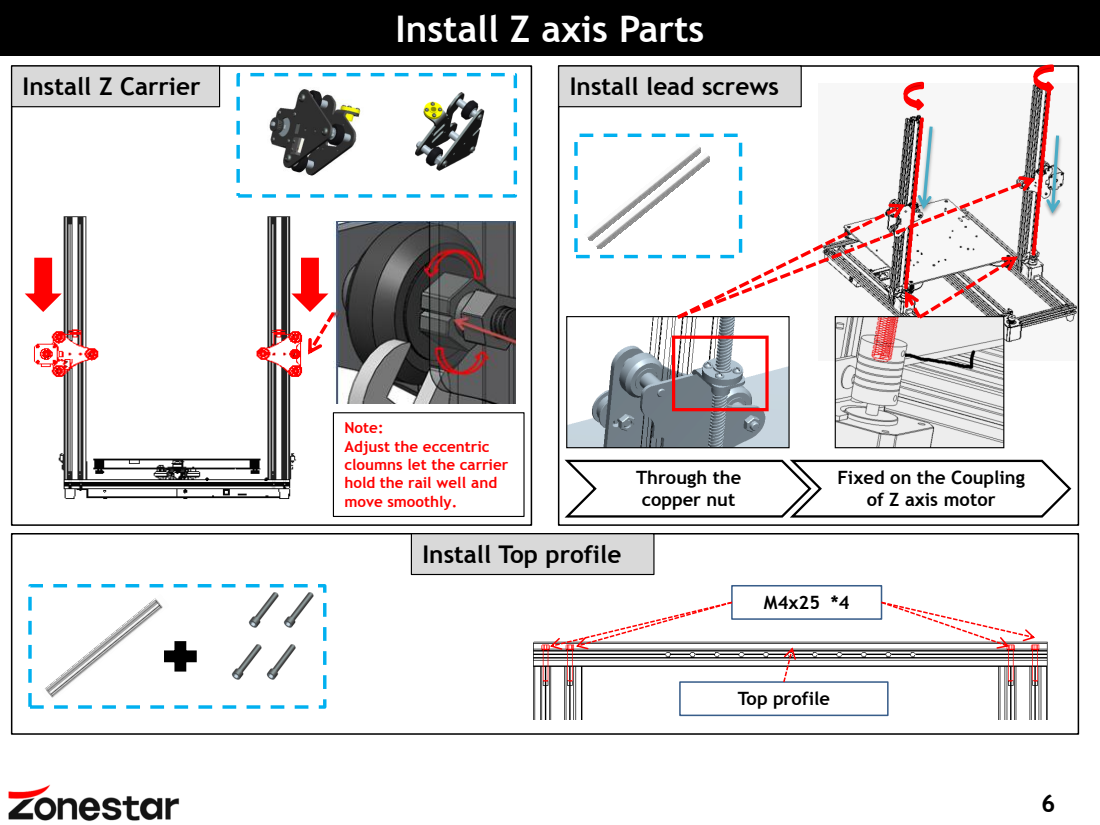
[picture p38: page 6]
Install Z Carrier; Install lead screws; Through the copper nut; Top profile

Note:
Adjust the eccentric
cloumns let the carrier
hold the rail well and
move smoothly.

Fixed on the Coupling
of Z axis motor

Install Top profile

# Install X axis Parts

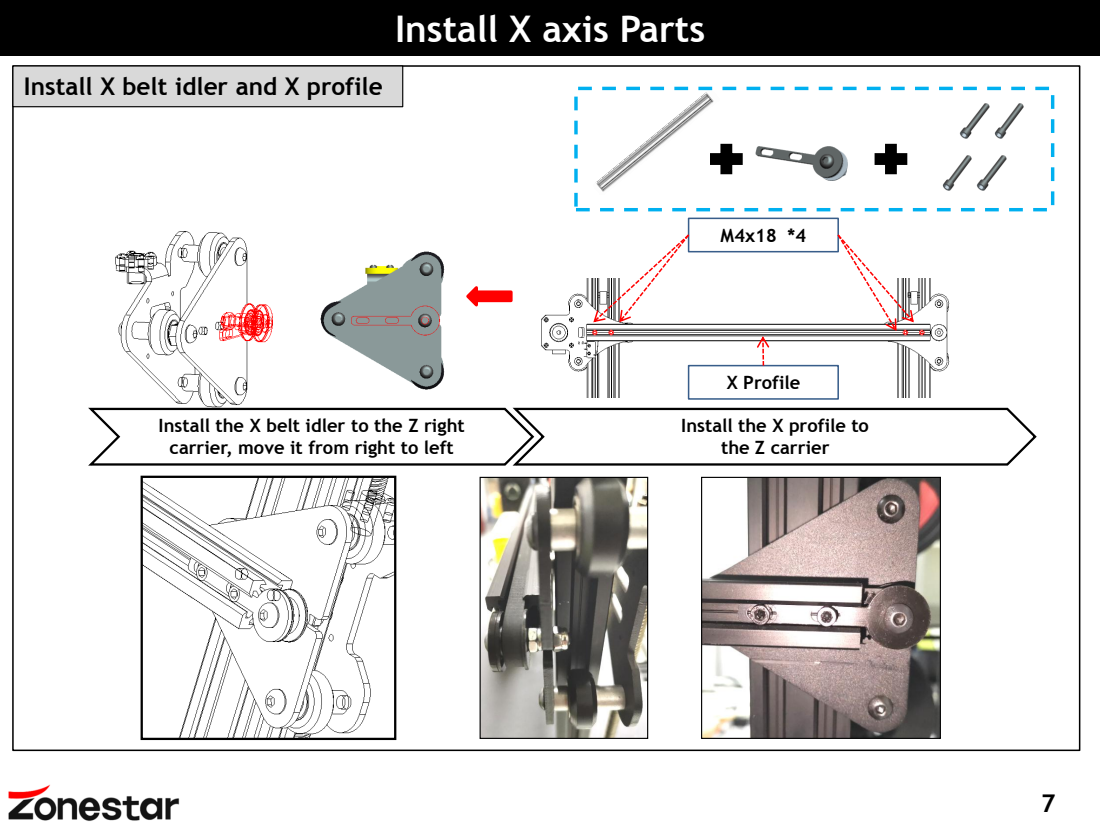
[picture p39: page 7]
X Profile

Install X belt idler and X profile

Install the X belt idler to the Z right
carrier, move it from right to left

Install the X profile to
the Z carrier

# Install X axis Parts

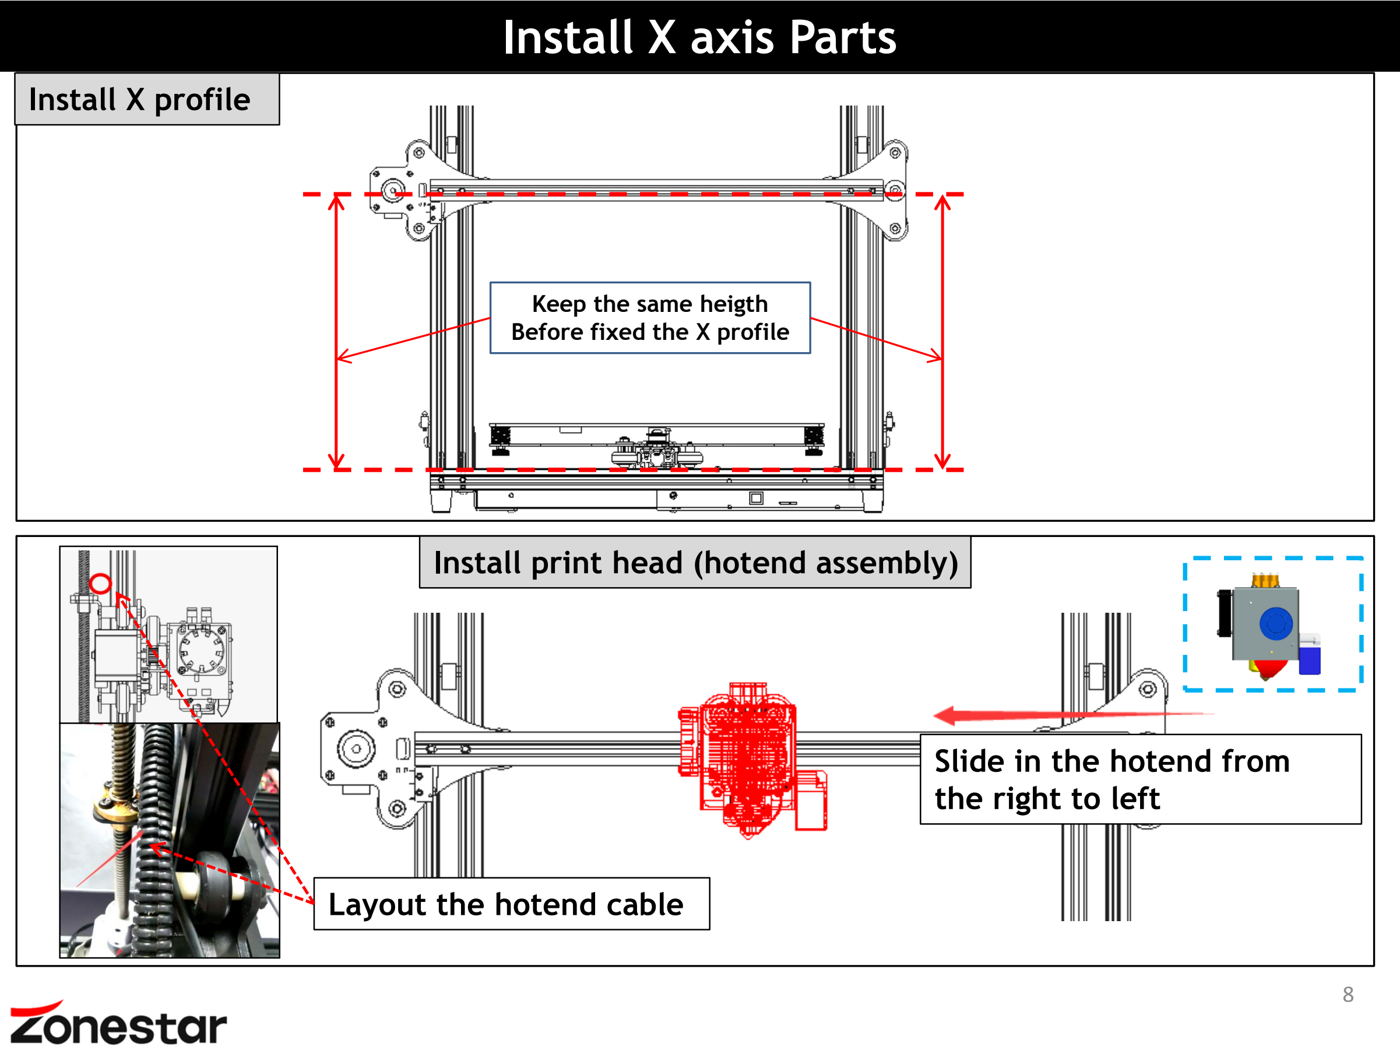
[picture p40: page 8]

Slide in the hotend from
the right to left

Layout the hotend cable

Keep the same heigth
Before fixed the X profile

Install X profile

Install print head (hotend assembly)

# Install X belt

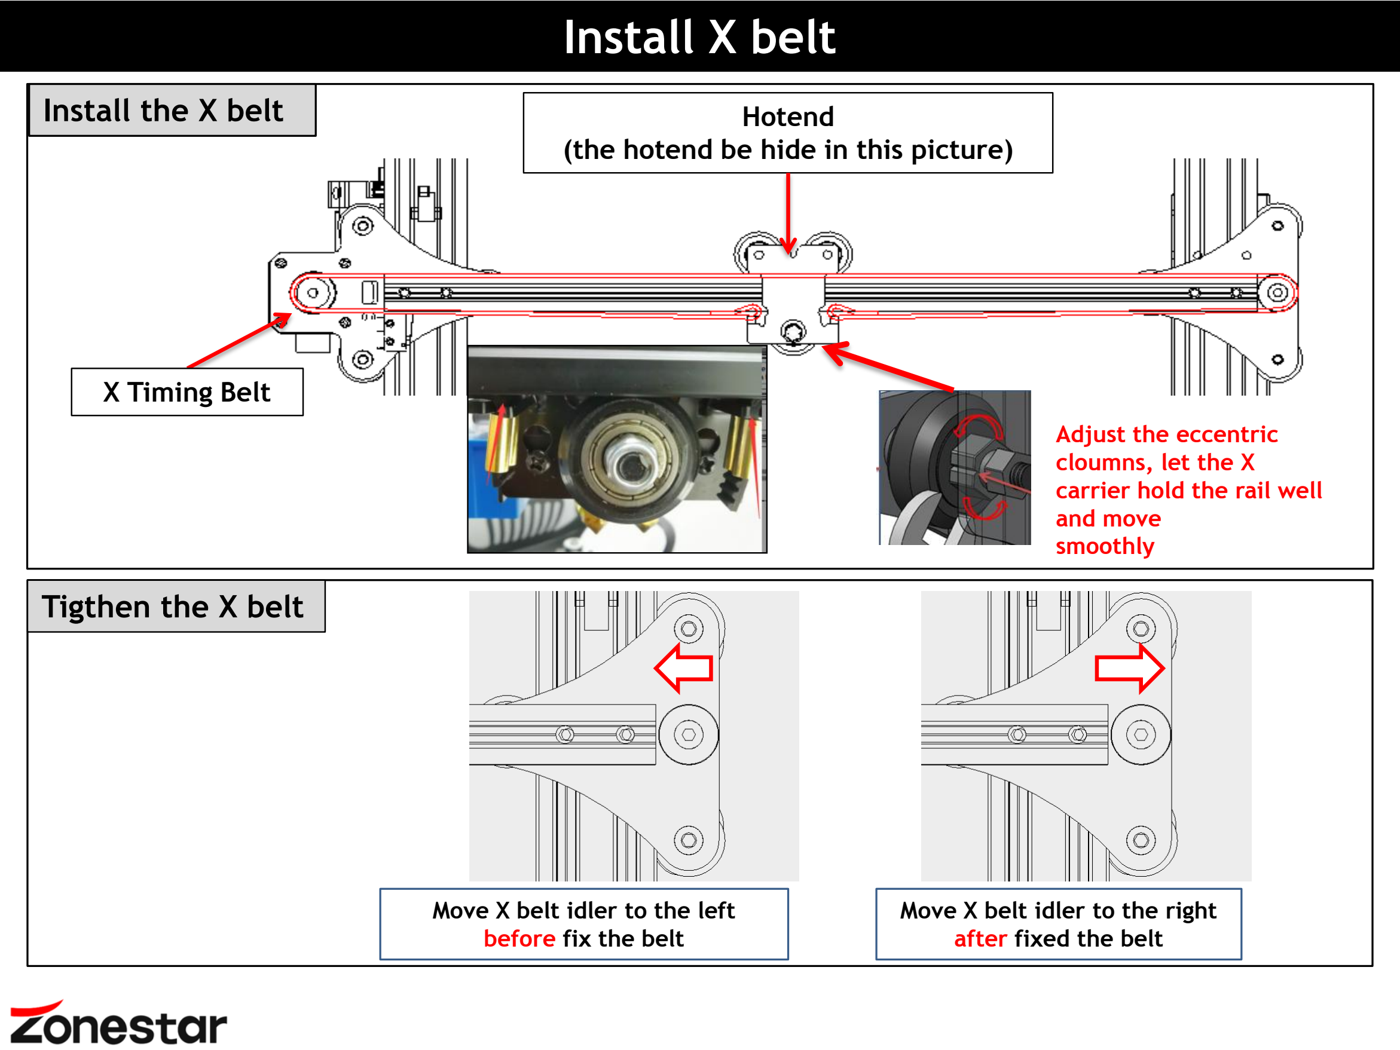
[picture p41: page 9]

Move X belt idler to the right after fixed the belt

Move X belt idler to the left before fix the belt

Tigthen the X belt

Install the X belt

X Timing Belt

Hotend
(the hotend be hide in this picture)

Adjust the eccentric
cloumns, let the X
carrier hold the rail well and move
smoothly

# Install the other parts

## x 3 o r 4

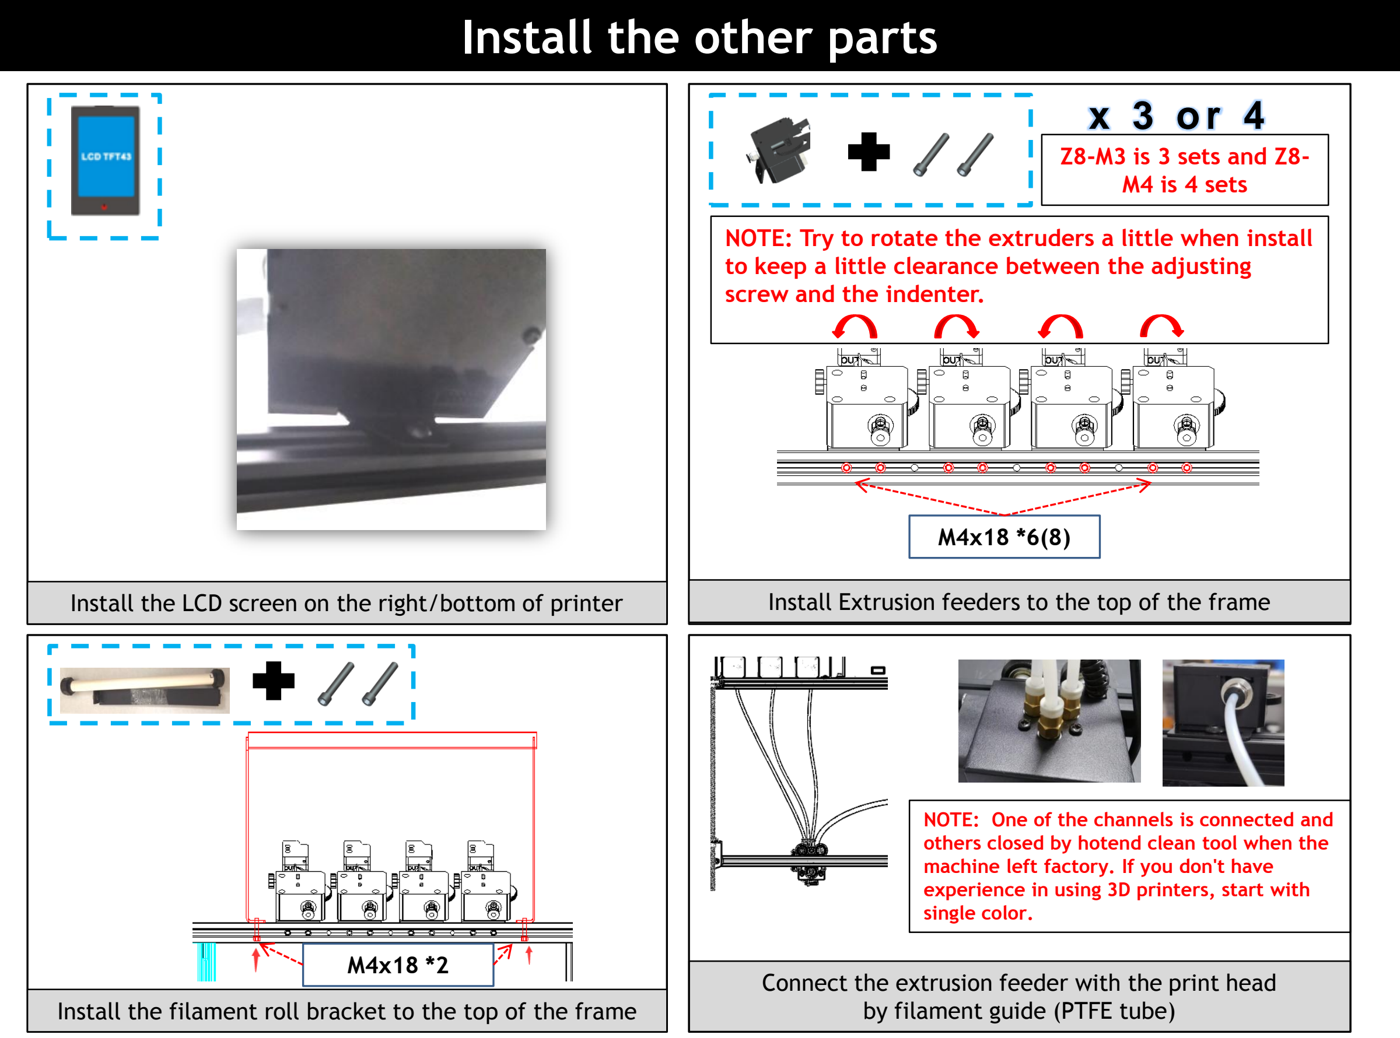
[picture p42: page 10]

Install the LCD screen on the right/bottom of printer

Z8-M3 is 3 sets and Z8-
M4 is 4 sets

Install the filament roll bracket to the top of the frame

Connect the extrusion feeder with the print head by filament guide (PTFE tube)

NOTE: One of the channels is connected and others closed by hotend clean tool when the machine left factory. If you don't have experience in using 3D printers, start with single color.

Install Extrusion feeders to the top of the frame

M4x18 *6(8)

NOTE: Try to rotate the extruders a little when install to keep a little clearance between the adjusting screw and the indenter.

M4x18 *2

Keep the lead screws parallel to the Z axis profiles as far as possible will help to obtain better printing quality, please debug them refer to the following steps: Step 1. Loosen all the screws a little that fixed the Z motors and T8 copper nut. Step 2. Synchronous Rotate the couplings to move up the X axis to 1/2 height of the printer. Step 3. Keep the lead screws parallel to the Z profiles, then tighten the screws that fixed the Z motor

| Loosen a little

and T8 copper nuts.
Step 4. Install the Z lead screws fix blocks on the top profile after done.

200mm

Put in

Fixed

Fixed

# Adjust height of Z ENDSTOPs

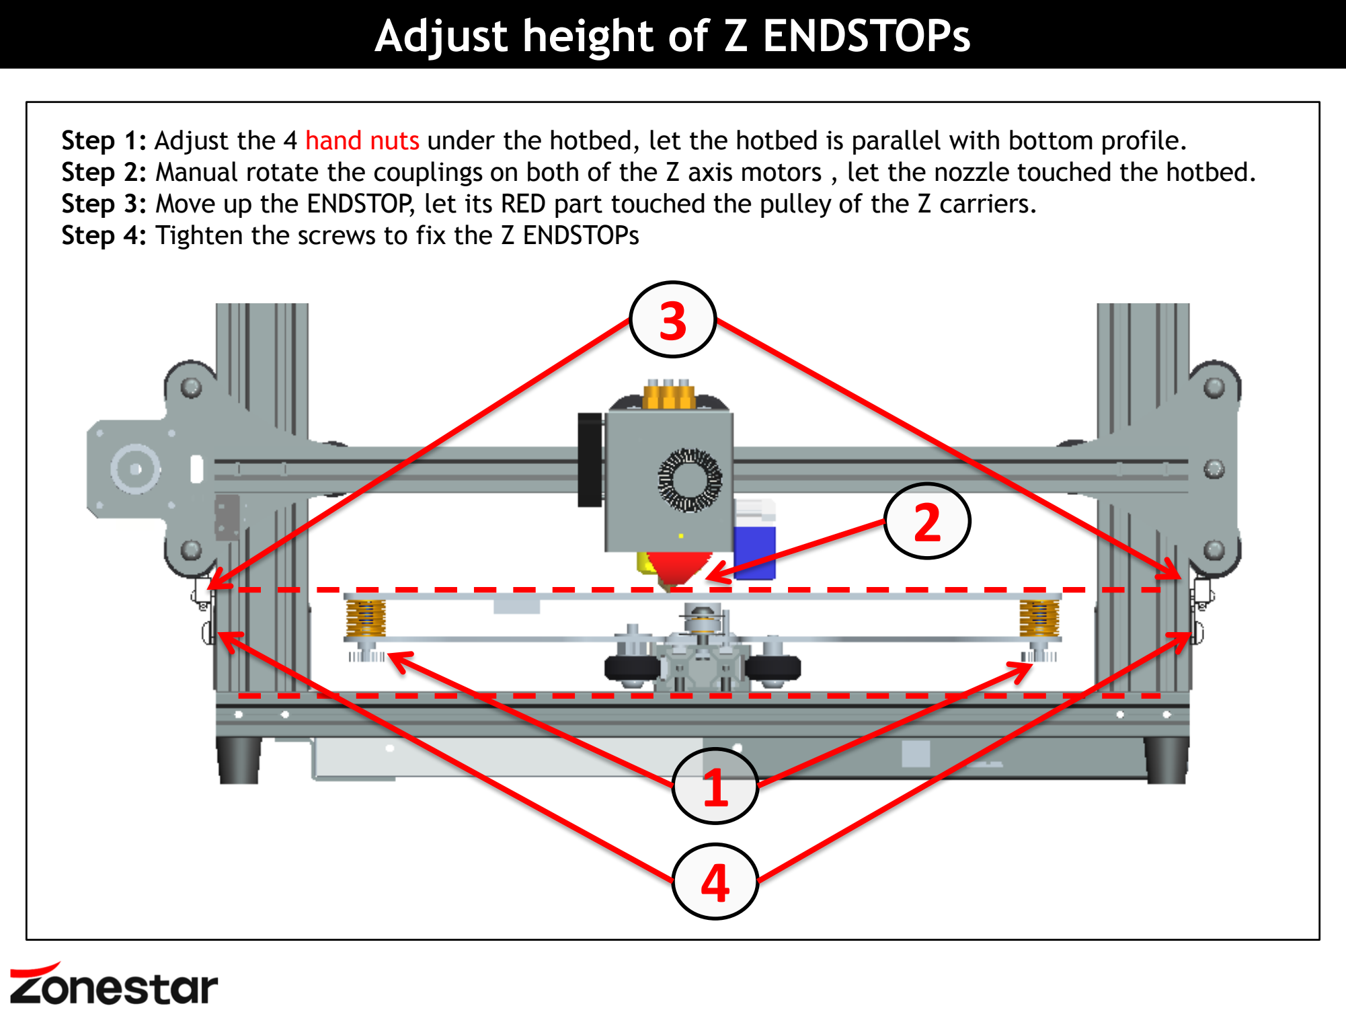
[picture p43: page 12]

Step 1: Adjust the 4 hand nuts under the hotbed, let the hotbed is parallel with bottom profile.
Step 2: Manual rotate the couplings on both of the Z axis motors , let the nozzle touched the hotbed.
Step 3: Move up the ENDSTOP, let its RED part touched the pulley of the Z carriers.
Step 4: Tighten the screws to fix the Z ENDSTOPs

1

2

4

3

## Take care when installation, to avoid electrical shock hazards!

## Double check the wiring! WRONG WIRING MAY DAMAGED THE ELECTRONIC DEVICE!

## Set the 110V/220V swicth (on the side of power supply) to correct position according to your city power voltage!

## Put the motor wire to the grooves of profile and cover them by

plastic profile cover, and using cable tie to wrap the free wires.

## Stop working immediately if the motor has abnormal vibration or noise,, otherwise the driver modules may be damaged!

## Make sure the hotend cooling fan is working when the nozzle

temperature is over 60 degree, otherwise check the wiring again.

## DC-IN, HOTBED has lager operating current, please make sure

these wires contact well with the terminal.

13

# About electronics parts

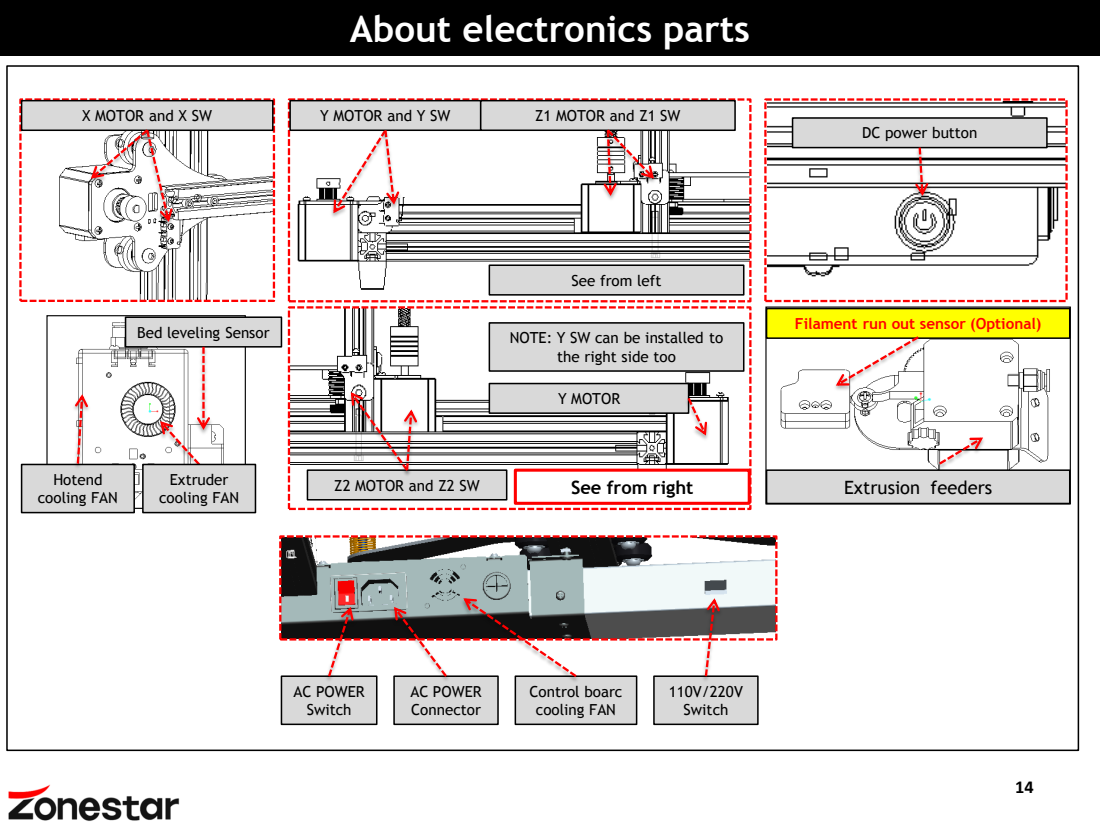
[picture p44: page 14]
X MOTOR and X SW; Y MOTOR and Y SW; Z1 MOTOR and Z1 SW; Extrusion feeders; Hotend cooling FAN; Y MOTOR; AC POWER Switch; AC POWER Connector; Control boarc cooling FAN; 110V/220V Switch; Extruder cooling FAN

DC power button

See from left

Filament run out sensor (Optional)

Bed leveling Sensor

NOTE: Y SW can be installed to

the right side too

Z2 MOTOR and Z2 SW

See from right

# Wiring Block

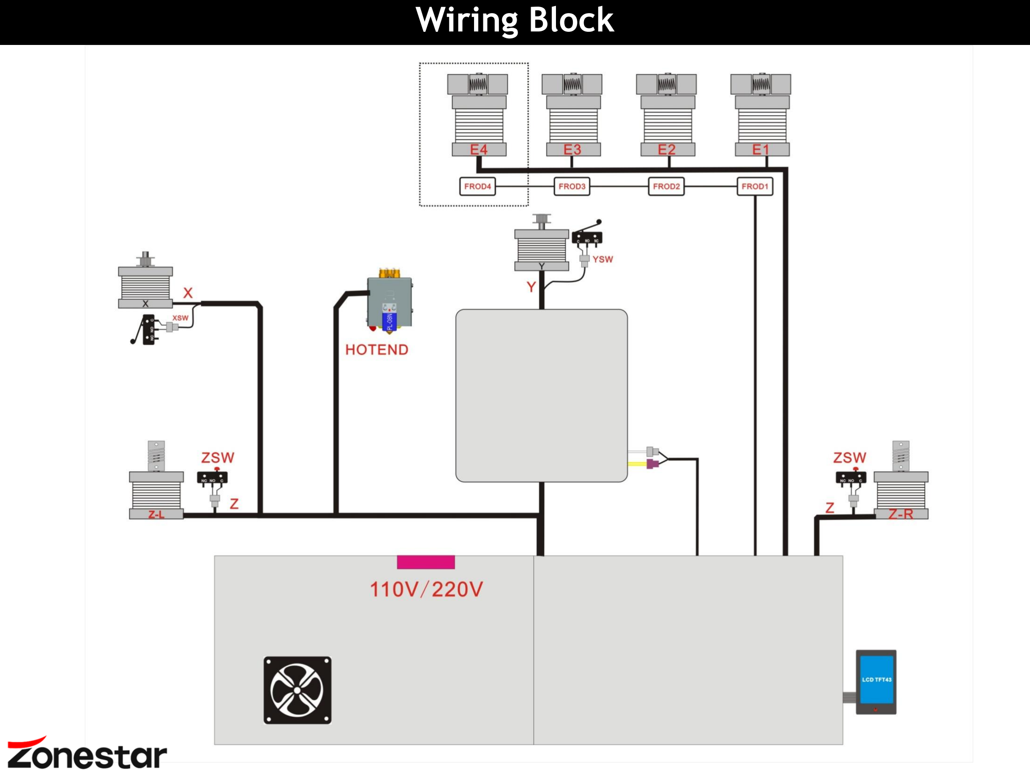
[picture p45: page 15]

# Layout the wires / cables

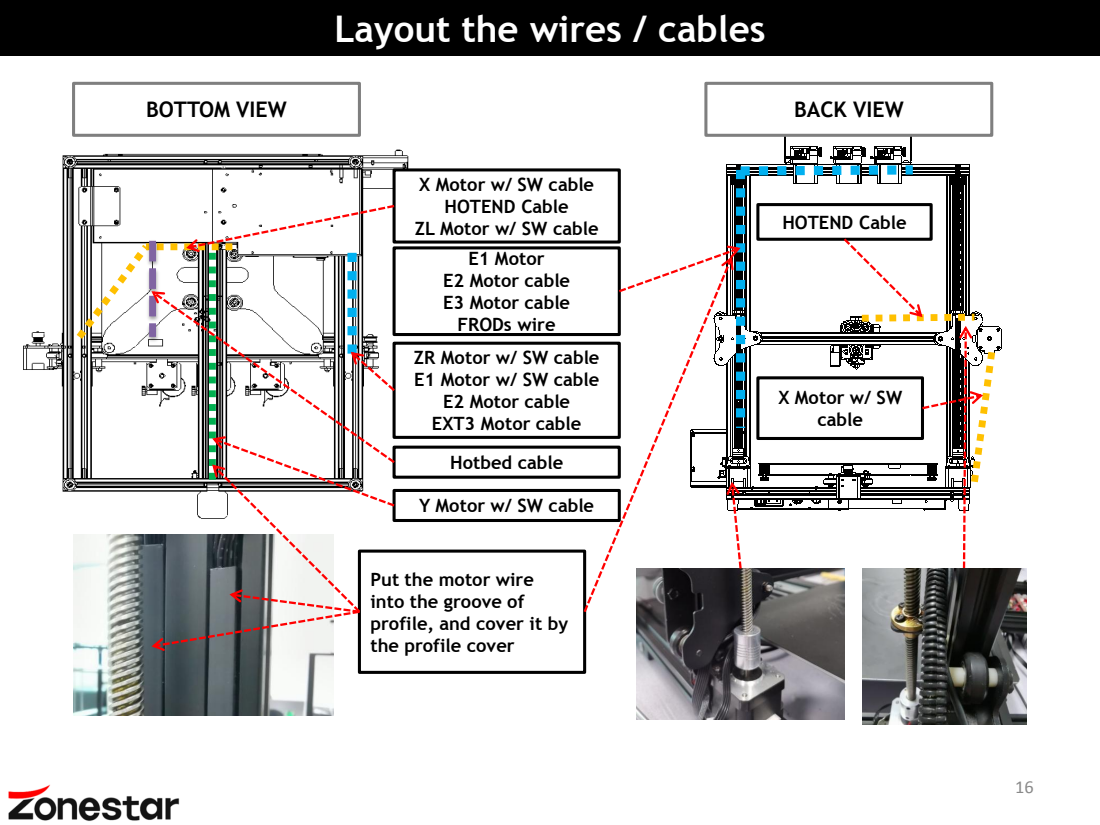
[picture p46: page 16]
Hotbed cable; BOTTOM VIEW; BACK VIEW; HOTEND Cable; X Motor w/ SW cable

X Motor w/ SW cable
HOTEND Cable
ZL Motor w/ SW cable

E1 Motor
E2 Motor cable
E3 Motor cable
FRODs wire
ZR Motor w/ SW cable
E1 Motor w/ SW cable
EXT3 Motor cable

Y Motor w/ SW cable

Put the motor wire
into the groove of
profile, and cover it by
the profile cover

Step 4: Manually move the hotend and hotbed to see if the movement is smooth, otherwise, adjust the eccentric nut until the motor moves smoothly. Refer to the installation procedure.
Step 3: Move the hotend and hotbed to their respective limit switch positions to check whether the contact is good and there is a clear sound. Otherwise, please check the limit switch and reassemble it.
Step 7: Manually rotate the z-axis screw rod to check whether the z-axis limit switch contacts reliably.
Step 5: Check whether the X and Y-axis drive belt is firmly installed. If it is too loose, please try to tighten it.

## It is very important to check the machine before power on. It can eliminate the trouble brought by some hardware to ensure the smooth printing!

Step 6: Check whether the screw rod is assembled in place and whether the screw is tightened
Step 1:Please check if the X&Y axis timing pulley are fixed on the shaft of motor, and the couplings are fixed on the shaft of the Z motors.
Step 2:Please check if the lead screws have been fixed on the shaft of coulping.

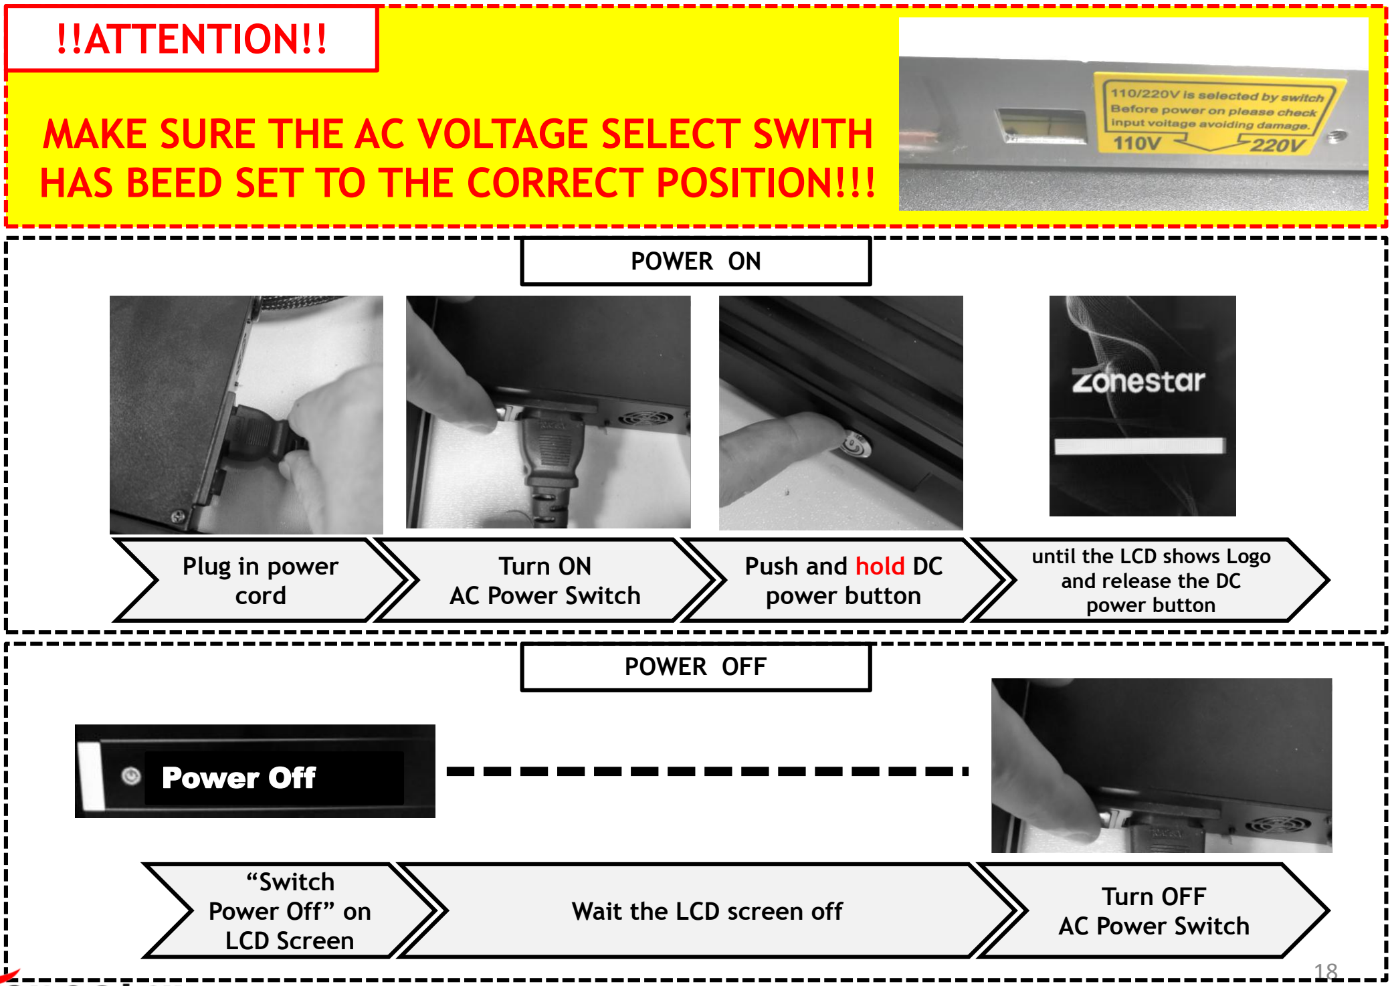
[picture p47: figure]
Wait the LCD screen off; POWER OFF; “Switch Power Off” on LCD Screen; Turn OFF AC Power Switch; Plug in power cord; Turn ON AC Power Switch; Push and hold DC power button; until the LCD shows Logo and release the DC power button; POWER ON; !!ATTENTION!!; MAKE SURE THE AC VOLTAGE SELECT SWITH HAS BEED SET TO THE CORRECT POSITION!!!; Power Off

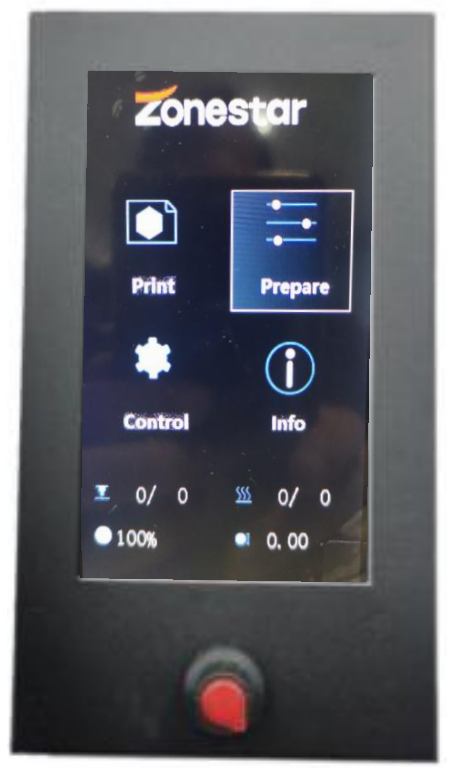
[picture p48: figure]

For details on the TFT-LCD menu, please refer to "LCD_DWIN Menu Description.pdf".

Printing from SD card

Prepare to printing

Setup the machine

Information of the machine Control handle

Title bar

Menu bar

Status bar

1. Power on the 3d printer and then do “Prepare>>Auto Home>>Home All” on control panel, wait the

hotend go to the HOME (origin) position.

2. Watch the nozzle, tighten the hand nuts under the bed to move down or loosen these nuts to move up

the bed (Fig 1), let the nozzle is higher than the bed about 1~2mm.

3. Do “Prepare>> Bed leveling>> Point 1(2/3/4)” on control panel(Fig 2), the nozzle will go to the

corners of the bed, adjust the hand nuts under the hotbed and let the nozzle almost touch the hotbed

(Fig 3). Continue to do the next point until all of the 4 corners has been leveled.

4. Repeat step 3 (recommend to do 3 rounds at least), until all of the four corners at the same height.


Fig 1 | Fig 2 | Fig 3

NOTE:


1. We have only open one channel of the hotend when the printer left the factory, so please load one filament the hotend in your first prints.
2. Before loading more than one filament to the hotend, please read this guide first “Mix Color HOTEND User Guide- load and unload filament.pdf” file in the SD card
1. Check the hotend, make sure only the center channel of the hotend connected “filament guide”

and the others channels has been closed by hotend clean tools (Fig 1).

2. Do “Prepare>>Auto Home>>Home All” on control panel, and then do repare>>Temperature>>

Preheat PLA”, waiting nozzle Temperature reached to 190 ℃ (Fig 2).

3. Use a diagonal pliers to cut off the head of filament (Fig 3), and then press the handle of the

extrude feeder #1 and insert filament, push the filament until you can see the filament in the

guide (Fig 4).

4. Rotate the gear of extrude feeder #1(Fig 5), watch the filament until it enter the hotend.

Continue to rotate the gear slowly and watch the nozzle, until you can see the filament flowed

out from the nozzle(Fig 6).

Fig 1 | Fig 2 | Fig 3 | Fig 4 | Fig 5 | Fig 6

1. Insert the SD card to the SD card socket on the printer (Fig 1).
2. Click “Print” on the control panel and choose “Test gcode\xyz_cube.gcode” (Fig 2), click the knob

to start printing.

3. Wait until the hotend and hotbed is reached to the setting temperature (Fig 3), the nozzle will

home to the origin position and then move to above of the printing platform and extrude the

filament, use a tweezers to remove the outflow filament (Fig 4).

4. Double click the knob on the control panel to open a “Babysteps” menu (Fig 5), rotate knob slowly

to fine tune the height of printing platform, watch the distance from nozzle to bed, until the

distance is well (Fig 6). Wait the printing finished, you will get your first works (Fig 7).

5. Wait the hotbed cool (<=25 degree) (Fig 8), and then remove the printed object from the hotbed

glass(Fig 9).


Fig 1 | Fig 5
Too far | Too close | Perfect

Fig 6

Fig 3

Fig 2 | Fig 4


Fig 7 | Fig 8 | Fig 9

# Slicing

About slicing
Slicing a 3D drawing translates the 3D drawing into a language that a 3D printer can understand and print. The slicing software is a computer software used in the majority of 3D printing processes for the conversion of a 3D object model to specific instructions for the printer. In particular, the conversion from a model in STL(Obj, Amf) format to printer commands in g-code format. This machine can use a variety of slicing software to complete slicing. We will now introduce the most commonly used slicing software: Cura.
NOTE: 1. Slicing software is not a part of this machine. 2. You can download Cura for free from the internet.

Install slicing software and step up the printer
In order to run the slicing software, you need a PC or laptabe, installed windows/linux/Macos.
Step 1: Download and install Cura to your PC, please search “ultimaker cura” from google.
Step 2: Copy “cura resources.zip” from the SD card and unzip it to your PC.
Step 3: Copy “resources” file to the same directory in cura which you installed.
Step 4: Run cura software, and follow the below steps to choose the printer.

Download
Cura

Download
Slicing Guide


Load stl files | Setup settings

Slicing and
preview

Store to SD
card

NOTE:
For description of slicing, please refer to the documents in the directory of “slicing”.

Slicing process

NOTE: Do not turn on these functions until you clearly understand how to use them and precautions.

- Bed auto leveling feature:
This printer is equipped with a Bed leveling sensor (PL-08N), with this sensor, you can correct the unevenness of the hot bed. . For the details please refer to the guide in “Bed Auto Leveling Feature”. Switch on: MENU>>Control>> Configre>> Auto Leveling
- Auto retract feature:
The strings issue of the mixed color hot end is often more serious than that of the single color hotend. Therefore, an automatic retraction feature is set in the firmware. Using automatic retraction can improve this problem. For the details please refer to How to set auto retract function.
- Filament run out detection feature (Filament run out sensor is an optional parts):
With these sensors, the printer can pause the printing while one of the filament spool used up, and when you load a new roll filament, you can continue to print. For the detail please refer to How to set filament runout function. Switch on: MENU>>Control>>Configre>>Runout Sensor
- Power loss recovery feature:
While printing from SD card and power is lost, after power on again, the printer will resume to print from the last layer which printed before power lost. For the detail please refer to Power loss recovery feature user guide.
Switch on: MENU>>Control>> Configre>>PowerLoss Recovery
- Auto power shut down feature:
While printing from SD card and the work is finished, the printer will auto shut down after about 3 minutes. For the details please refer to How to set auto shutdown function.
Switch on: MENU>>Control>> Configre>> Auto Shutdown

## You can print something to upgrade your printer, we have made some printed part

and store the stl file to the SD card, you can feel free to slicing it and print it out, and then install them to your kit to make the printer better.


cap_af_20v.stl | cap_af_40v.stl

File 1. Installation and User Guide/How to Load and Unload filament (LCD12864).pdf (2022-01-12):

## 混色热端进料退料和换料操作手册

## How to Load/Unload Filament for Mixing Color HOTEND

## как загружать и перевозить цветные горячие концы накала

## Cómo manipular un filamento térmico mezclado

## Como Carregar/Descarregar o Filé para Misturar Cor HOTEND

## Comment charger et décharger un fil d 'extrémité thermique mélangé

# How to unload filament

- 第1步，加热喷嘴并等待温度到达,PLA是220度,ABS/PETG是250度 (Fig 1)

### - 第2步: 操作菜单手动挤料直至耗材顺利从喷组流出 (Fig 2)

- 第3步: 操作菜单选择“Unload filament E1/E2/E3/E4”,然后压住挤出机手柄并拔出耗材(Fig 3)
- Step 1: Heating the nozzle, PLA to 210 degree ABS to 250 degree. (Fig 1)
- Step2: Purg a little filament from all extruders, until the filament can flow out from nozzle well. (Fig 2)
- Step 3: Do “Unload filament E1/E2/E3/E4” from LCD MENU，then pull out filament from extrusion feeder. (Fig 3)
- первый шаг: нагревательная форсунка, PLA до 210 градусов ABS до 250 градусов. (Fig 1)
- Второй этап: выжать немного волокна из всех экструдеров до тех пор, пока волокна не будут вытекать из сопла. (Fig 2)
- Этап 3: выполнение “Unload filament E1/E2/E3/E4”. вытащить нить накала из экструдера. (Fig 3)
- Primer paso: toberas de calentamiento, de PLA a 210 grados ABS a 250 grados. (Fig 1)
- Segundo paso: sacar un poco de fibra de todas las máquinas de desplazamiento hasta que las fibras puedan salir por la abertura de la tobera. (Fig 2)
- Tercera etapa: ejecución del “Unload filament E1/E2/E3/E4” ， sacar la luz del encuadernador. (Fig 3)
- Passo 1: Aquecimento do bocal, PLA a 210 Grau ABS a 250 grau. (Fig 1)
- Step2: Purgar um pouco de filamento de todos OS extrusores, até que o filamento possa sair do poço do bocal. (Fig 2)
- Passo 3: Executar “Unload filament E1/E2/E3/E4”. Retirar o filamento do alimentador de extrusão. (Fig 3)
- Première étape: Tuyères de chauffage, PLA à 210 degrés ABS à 250 degrés. (Fig 1)
- Deuxième étape: Extruder une petite quantité de filaments de toutes les extrudeuses jusqu 'à ce que les filaments sortent de l' orifice de buse. (Fig 2)
- Étape 3: mise en œuvre du menu LCD “Unload filament E1/E2/E3/E4”. étirez les fils du four d 'extrusion. (Fig 3)

# How to load filament

- 第1步，加热喷嘴并等待温度到达,PLA是220度,ABS/PETG是250度(Fig1)

### - 第2步，使用热端清理工具关闭未使用的热端的通道(Fig4) - 第3步，使用斜口钳剪将耗材头部剪成斜口(Fig5) - 第4步, 压住挤出机压头并将耗材插入,并一直将耗材送入热端内部(Fig6) - 第5步, 如果需要同时装入多种耗材,重复3和4 - 第6步, 操作菜单手动挤料直至耗材顺利从喷组流出. (Fig3)

- Step 1: Heating the nozzle, PLA to 210 degree ABS to 250 degree. (Fig1)
- Step 2: Use the hotend clean tool to close ununsed channel. (Fig4)
- Step 3: Cut the head of the filament with a slant cutter. (Fig5)
- Step 4: Press the handle of extrusion feeder and insert the filament until it enter the hot end. (Fig6)
- Step 5: Repeat step 3 and 4 if you need to load more than one filament at the same time
- Step 6: Purg filament from all extruders, until the filament can flow out from nozzle well. (Fig3)
- первый шаг: нагревательная форсунка, PLA до 210 градусов ABS до 250 градусов. (Fig1)
- Шаг 2: Закрытие неиспользованных каналов с помощью утилиты горячей очистки. (Fig4)
- Третий этап: резать патрон накала косым резаком. (Fig5)
- шаг четвертый: нажать рукоятку экструдера, вставить нить накала в горячий конец. (Fig6)
- Шаг 5: если необходимо одновременно загружать несколько нить накала, повторить шаги 3 и 4
- шаг шестой: экструзия из всех экструдеров длинных шёлков до тех пор, пока длинный шёлк не истечет из соплового отверстия. (Fig3)

# How to load filament

- Primer paso: toberas de calentamiento, de PLA a 210 grados ABS a 250 grados. (Fig1)
- Medida 2: utilización de instrumentos de depuración de calor para cerrar canales no utilizados. (Fig4)
- Tercer paso: cortar la lámpara con un cortador oblicuo. (Fig5)
- Cuarto paso: presionar para sacar el mango del horno e insertar la lámpara en el extremo caliente. (Fig6)
- Medida 5: repetición de las etapas 3 y 4 si es necesario introducir simultáneamente varios filamentos
- Sexto paso: sacar alambre largo de todas las máquinas de desplazamiento hasta que el alambre pueda salir por la abertura de la tobera. (Fig3)
- Passo 1: Aquecimento do bocal, PLA a 210 Grau ABS a 250 grau. (Fig1)
- Passo 2: Use a ferramenta de limpeza hotend para Fechar o canal não aberto. (Fig4)
- Passo 3: Corte a cabeça do filamento com um alicate inclinado. (Fig5)
- Passo 4: Pressione o cabo do alimentador de extrusão e insira o filamento até Entrar Na extremidade Quente. (Fig6)
- Passo 5: Repetir o Passo 3 E 4 se você precisar carregar Mais de um filamento Ao Mesmo tempo.
- Passo 6: Extrair filamento de todos OS extrusores, até que o filamento possa sair do poço do bocal. (Fig3)
- Première étape: Tuyères de chauffage, PLA à 210 degrés ABS à 250 degrés. (Fig1)
- Étape 2: fermer les canaux inutilisés au moyen d'un outil de nettoyage d'extrémité thermique. (Fig4)
- Étape 3: couper le fil avec un coupe - lames. (Fig5)
- Étape 4: appuyer sur la poignée du four d 'extrusion et insérer le fil dans l' extrémité chaude. (Fig6)
- Étape 5: répéter les étapes 3 et 4 si plusieurs filaments doivent être chargés simultanément
- Étape 6: Extruder les filaments de toutes les extrudeuses jusqu 'à ce qu' ils sortent des orifices de buse. (Fig3)

# How to load/unload filament

## MENU>>temperature


PLA: 220
ABS /PETG: 250
MENU>>Motion>>Move axis | (Fig1)
M3 = 3 M4 = 4 | 30 ~ 100

## (Fig 2)

## (Fig 3)

# How to load/unload filament


(Fig 4) | (Fig 5)

## (Fig 6)

## Enter 50mm

50mm

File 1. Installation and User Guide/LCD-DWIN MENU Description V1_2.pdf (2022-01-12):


# DWIN LCD MENU Description

1

# Version: 1.2

# •Main Menu

LOGO; Title

Print from SD card | Contrll for Prepare to print

Printer Setting | Printer Information

Nozzle Temperature | Hotbed Temperature

Printing Speed | Current Z position

# •Printing status Menu

Printting controller; Title

Printng file name and Progress bar

Extruder Mix Rate and Auto Mixing mode

Printed timer and Remain timer

Setting | Printing | Stop Printing Pasue&Resume

Nozzle Temperature | Hotbed Temperature

Printing Speed | Current Z position

Status Message Bar

# Prepare

Auto Home; Temperature; Move; Filament; HOME ALL; HOME X/Y/Z axis; Move X/Y/Z; Extruder1/2/3/4; ExtruderAll; Extruder; Slowly length; Quickly length; Preheat nozzle; Preheat the nozzle to 200 degree; Slowly Load; Slowly UnLoad; Quickly Load; Quickly UnLoad

HOME all axis at once

HOME ALL HOME X/Y/Z

For Z9 , it will do HOME Y first even you HOME X

Hotend Temp
Hotbed Temp
Fan Speed
PreHeat PLA
PreHeat PLA/ABS
Cooldown

Set hotend(Nozzle) Temperature
Set Hotbed Temperature
Set Extuder Cooler FAN speed
Set Nozzle/Hotbed/Fan at once
See the menu “control >>Preheat PLA/ABS”
Turn off Nozzle/Hotbed/Fan at once

Move X Y or Z axis
Move extruder(1~4) motor
Move all extruder motors
at the same time

Choose which extruder you need to load filament

how long filament be Load/Unload
when clicked “Slowly Load/Unload”
when clicked “Quickly Load/Unload”
Load/Unload filament slowly

Load /Unload filament quickly

see the nex page

Bed Leveling; Language; DisableSteppers; Power off; Prepare; Point1/2/3/4; Catch Z-offset; Probe Z-Offset; Auto leveling; Mixer; Control; Mix; Current V-TOOL; Set current(working) V-TOOL

Do leveling at the bed corners

Auto Catch the probe Z offset
Set the probe Z offset
Do auto leveling measure

Display only
when “Auto
levleing” is ON
Refer to configre

Auto leveling EN/PT/ES/FR/RU

Set menu language

Turn off the power supply to motors

Power off the printer

Set mix rates of each extruder and commit to V-TOOL
Start a Gradient mix printing and set paremeters
Start a Random mix printing and set paremeters

Gradient (ON/OFF)

Random (ON/OFF)

see the nex page

# Control

## Runout Sensor

Motion; Feedrate; Acceleration; Jerk; Step/mm; Store Settings; Or reset to default Store/Load Settings /Retore Defaults; Configre; Auto Retrac; Auto Shutdown; Turn ON/OFF idel auto shut down feature; WiFi BaudRate; Set WiFi BaudRate (Need restart printer to apply it)

Set Auto Retraction parameters
Turn ON/OFF filament run out detection
Turn ON/OFF Power lost Recovery feature

PowerLoss Recovery
WiFi
Home Z offset
Auto Leveling
Active Auto Level

Turn ON/OFF WiFi feature

Set the Z HOME offset

Turn ON/OFF bed auto leveling feature
Active bed auto leveling correct when printing

Set printing speed limiting parameters
Set acceleration limiting parameters

Set Jerk parameters

Set Steps/mm parameters of stepping motors

Nozzle/Bed Temp
Fan Speed
Store Settings

Set nozzle/Bed temperature and FAN speed
when do “Preheat PLA” in Prepare menu

Preheat PLA/ABS

Store the setting quickly

Save /Apply the setting

## Speed

# Tune

Hotend Temp; Bed Temp; Fan Speed; Z Offset; Mixer; configure; BabySteps; BabySteps menu; Menu

Tuen menu only disply when print from SD card

Tune the ratio of printing speed

Tune Nozzle temperature

Tune bed temperature

Tune Extruder FAN Speed

Tune nozzle (or Bed) height

Double click the knob twice with in one second will open

Tune mixer settings, refer to “Control>> Mixer” Menu

Tune ON/OFF some features, refer to “Control>> Configure”

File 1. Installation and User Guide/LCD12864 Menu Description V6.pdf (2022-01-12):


# Brief of LCD Menu ZONESTAR 3D Printer DIY Kit

# (Base on Marlin 2.0.x)

# Ver: 6


# LCD screen and Keypad

LCD12864 with knob

## Operation and Function

Operation | Function
Clockwise rotation | Menu item+ / Value +
Counterclockwise rotation | Menu item+ / Value -
Push | Open Menu /Enter


fig | Description
1 | Current hotend temperature
2 | Setting hotend temperature
3 | Current hotbed temperature
4 | Setting hotbed temperature
5 | Current X Y Z position
6 | Extrude fan speed
7 | Multiple of print speed
8 | SD card print progress
9 | Status message
10 | mix rate of extruders
11 | Current Virual Tool Number or Auto Mix Mode

State menu description

# Menu description

Menu | Sub-Menu | Description | Remark
| Info Screen | Return to info menu
| Motion | Prepare Menu | Only shows on ideal status
| Pause Print | Pause Printing | Only shows on printing
| Stop Print | Stop Printing | Only shows on printing
| Tune | Tune parameter when printing | Only shows on printing/Motion
| Temperature | Control Menu
| Mixer* | Mixing Settings | Only available in mixing printer.
| Configuration | Set the printer parameter
| Change Filament | A wizard to help change filament
| About printer | Printer infomations
| Change Media | Press it before remove the SD card from control board | Only shows on ideal status
| Switch Power off | Power off the printer (only control board) | Only available has power button
| Print From Media | Press it to start to print from SD card. | Only shows on ideal status
Pop Menu | Babystep Z | double click the knob to open when printing | Only available when printing

Main Menu

*:

# Menu description

Motion

| Move Axis | Move X/Y/Z/Extruder motor | Need to heat nozzle before moving extruder
| Auto HOME | Do homing for all X/Y/Z
| HOME X/Y/Z | Homing X/Y/Z separately
| Bed Leveling | Bed leveling feature
| >>Level Corners | Move the nozzle to near the corners of hotbed | Adjust the screws under the bed to level it
| >>Catch Z probe offset | Catch the probe Z offset
| >>Level bed | Do a bed auto levling processing | Only for bed leveling sensor installed
| >>Probe Z offset | Adjust probe Z offset
| >>Bed leveling: Off(ON) | If a Bed leveling has done | Apply the Z axis error when show “ON”
| Disable Steppers | Turn off the power of stepper motors
Temperature | Nozzle | Set nozzle temperature
| Bed | Set bed temperature
| Fan Speed | Set extruder FAN speed | Cooling fan is control automatically
| Preheat PLA/ABS | Preheat the hotbed and/or hotbed
Mixer | Active V tool | Set the current work V Tool | These menu only showed when the printer has mixing feature, about the detail, please refer to the mixing feaure user guide.
| Mix | Set Mixing parameter setting
| Gradient: disable | Set Gradient mixing parameters
| Random Mix: disable | Set Random mixing parameters

# Menu description

Configuration

| Advanced Settings
| Run out sensor: On/Off | Turn on/off the filament run out detection feature | * Refer to “Filament Run out feature”
| Outage Recovery: On/Off | Turn on/off power loss recover feature | * Refer to “Power loss Resume feature”
| Preheat PLA/ABS Conf | Set preheat parameters
| Store Settings | Store the configuration to NVRAM of control board | Do it after you modified parameter!
| Load Settings | Load the NVRAM setting to the printer
| Restore Default | Reset the setting to the default
Tune | Speed | Adjust the print speed | Percentage of speed based on gcode
| Nozzle | Nozzle temperature
| Bed | Hotbed temperature
| Fan Speed | Extruder fan speed
| Flow | Extruder flow rate | Percentage of flow
| Babystep Z | Fine tune the Z height

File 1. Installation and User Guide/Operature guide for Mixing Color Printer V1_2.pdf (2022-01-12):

# Operation Guide for Mixing Color printer

V1.2

# Symbols

•Extrusion feeder: A mechanism to transport filament to the hotend.
•Hotend: The part to melt and eject filament.
•Nozzle: The outlet at the front end of the hotend, usually made of copper, use the size of the front hole to describe its main size.
•Print head: The hotend and its attached cooling system.
•Control panel: The system that realizes human-machine interface in 3D printer.
•Mixer: The parts and software to realize the color mixing function.
•Mixing Extruder: An extruder that can mix different color filament together.
•Channel of Hotend: The channel through filament enter into the mixing hotend.
•Tool Chain (Tool head): In short, one tool chain corresponds to one printing color, in most slicing software, tool chain is also be called extruder. For singel color or general multicolor printer, each extrusion feeder corresponds to one hotend/nozzle, so the number of tool chain is equal to the extrusion feeder and nozzles. For mixing color printer, because the same hotend can print different colors, so we can set many tool chains.
•Virual Extruder / Virsual Tool Chain:
In mixing color extruder, multiple extrusion motors correspond to one nozzle. One combination of extrusion rates can correspond to one tool chain. In order to distinguish them from single color and simple multi color 3d printer, they are called Virsual Tool Chain.
•Gradient Mixing:
A function of automatic color mixing transformation processing. When starting a print file from SD card (slicing it with single color), it will automatically adjust the mixing ratio of extruder according to the preset ratio (preset virtual extruder) when the printing height changes, so as to realize a Gradient color effect.
•Random Mixing:
A function of random color mixing transformation processing. When you start a print file from SD card (slicing it with single color), it will randomly adjust the mixing ratio of extruder when the printing height changes, so as to realize a Random color effect.
•Hotend Clean tool:
A screw with a small rod which can be used to clean the feeding channel at the hot end, or to close the temporary non feeding channel.

# Principle and structure of hotend

- Different more than one color filaments are fed into the HOTEND by extrusion feeder, they are melted in the heat block and mix together and then flow out from nozzle. By adjusting the feeding ratio of extrusion feeder, we can get different color filament from the nozzle. Fittings (PC04-M6)

hold the PTFE tube on the hotend

Heat sink
Connect the hotend to the printer keep the inner PTFE tube is cool

Inner PTFE tube (Ø4x2 High temperature resistance PTFE tube) Isolation the throat with filament to keep the filament cool

Filament guide(Ø4x2 PTFE Tube) Connect hot end and extrusion feeder, filament inside

Throat (HM3 V2 and V3 use MK10 type) Connect the heating block with the heatsink

Heating block
Melting and Mixing the filament
(Use 50W heater and NTC100K B3950 temperature)

Nozzle
Filament flow from here
- Since the individual channels are ultimately connected, the filament may flow backwards into the empty channel, which can cause the empty channel be clogged. Therefore, we must insert filament or use "HOTEND clean tool" to close the unused channel to prevent the melted filament to reflux.
- Because there is a color mixing cavity inside hotend, when switching extruder, it does not immediately switch to the desired color.
- Keep the heatsink to cool is very important, otherwise the filament can't be push to the nozzle well, it will cause the clogged issue, make sure the cooling FAN working when nozzle temperature is over 60 degree.
- PC04-M6 fitting is easy to break,do not use a wrench to tighten it.

HOTEND CLEAN TOOL

NOTE: This figure is a schematic illustration of the principle, actual structure may different!!

# !!ATTETION!!

1. Load filament to all channels; DONOT load / unload filament when the nozzle temperature is less than150 ℃

DONOT feed-in filament over 10mm if any of the channels is empty, otherwise may cause it be clogged. you can:

2. Use a hotend clean tool to close empty channels.

# How to print singel color 3d object


Step 1: Refer to the silcing guide for mixing color printer to covert the 3d mode file to gcode file. Step 2: Preheat the nozzle to about 170 degree
Step 3: Use hotend clean tool to close the unused channle of hotend
Step 4: load filament to the hotend. NOTE: For M4 printer, recommend to load the filament to the center channel. Step 5: print gcode file from SD card

# Change printed color by adjust mixing rate (LCD12864)


Step 1. Start to print a singel color gcode file(Vase.gcode) from SD card. Step 2. For LCD12864 screen, set on the menu>>

●Mixer>>Active V-tool: Select the vtool currently printed, or use the default value, the range is 0 ~ 15. ●Mixer>>Mix>>Component1~4(M4): Arbitrarily adjust the percentage of extruder 1 ~ 4, the range is 0 ~ 100. ●Mixer>>Mix>>Comit V-tool Mix: Redistribute the percentage of all extruders in proportion

and send it to the current vtool. After setting up, on the ideal menu shows VTOOL:0


# Hot to Change printed color by adjust mixing rate (LCD-DWIN)

Step 1. Start to print a singel color gcode file(Vase.gcode) from SD card. Step 2. For TFT screen, set on the menu>>

●Mixer>>Current V-TOOL: Select the vtool currently printed, or use the default value, the range is 0 ~ 15. ●Mixer>>Mix>>Extruder1~4(M4): Arbitrarily adjust the percentage of extruder 1 ~ 4, the range is 0 ~ 100. ●Mixer>>Mix>>Comit V-tool: Redistribute the percentage of all extruders in proportion and send it to the

current vtool. The current vtool value changes color. After setting up, enter printing, on the printing menu shows: Mix 0


# How to realize gradient printing(LCD12864)

Step 1. Start to print a singel color gcode file(Vase.gcode) from SD card. Step 2. For LCD12864 screen, set on the menu>>

Mixer>>Gradient: disable >>


Start Z: set the start Z heigth(such as:0mm) End Z: set the END Z heigth(such as:200mm) Start V-tool: set the start V-tool(such as:0) End V-tool: set the end V-tool(such as:1) After set Start Z isn’t equal to the End Z, and Start V-tool isn’t equal to End V-tool, the LCD will shows “Gradient : enable” and on the ideal menu shows gradient


# How to realize gradient printing(LCD-DWIN)

Step 1. Start to print a singel color gcode file(Vase.gcode) from SD card. Step 2. For LCD-DWIN screen, set on the menu>>

Mixer>>Gradient: OFF >>
Start Z: set the start Z heigth(such as:0mm) | End Z: set the END Z heigth(such as:200mm)
Start V-tool: set the start V-tool(such as:0) | End V-tool: set the end V-tool(such as:1)
After set Start Z isn’t equal to the End Z, and Start V-tool isn’t equal to End V-tool, the LCD will shows “Gradient : ON” and on the printing menu shows: Gradient 0--->1


# How to realize random printing(LCD12864)

Step 1. Start to print a singel color gcode file(Vase.gcode) from SD card. Step 2. For LCD12864 screen, set on the LCD menu>>

Mixer>>Random Mix: disable >>


Start Z: set the start Z heigth(such as:0mm) End Z: set the END Z heigth(such as:200mm) Height: set interval distance(such as:10mm)

Extruders: set the number of extruders with random variation(such as:4)
After set Start Z isn’t equal to the End Z, the LCD will shows “Gradient : enable” and on the ideal menu shows random


# How to realize random printing(LCD-DWIN)

Step 1 Start to print a singel color gcode file(Vase.gcode) from SD card. Step 2. For LCD-DWIN screen, set on the menu>>

Mixer>>Random: OFF >>
Start Z: set the start Z heigth(such as:0mm) | End Z: set the end Z heigth(such as:200mm)

Height: set interval distance(such as:10mm)

Extruders: set the number of extruders with random variation(such as:4)
After set Start Z isn’t equal to the End Z, the LCD will shows “Random : ON” and on the printing menu shows: Random


# Hot to print multi-color 3d object

Step 1: Refer to the silcing guide for mixing color printer to covert the 3d mode file to gcode file. Step 2: Preheat the nozzle to about 170 degree
Step 3: Load filament to the hotend, and use hotend clean tool to close the unused channles
Step 4: print gcode file from SD card(4C_Niko_Dog.gcode)

TIPS 1:; the extruder PS: Their sequence depends on wiring; TIPS 3: The steps to load filaments:

Make a mark on the extrusion feeder in order to quickly distinguish

TIPS 2: Recommended channels for different quantities of filaments


1. Heat nozzle, and then use hotend clean tool to close unused channel (remove the fittings first)!
2. load all of the filaments into the hotend, stop when it enter the hotend about 30~40mm. 3. MENU>>Motion>>Move axis>>Set V-TOOL to 3(for M3) or 4(for M4). 4. MENU>>Motion>>Move axis>Extruder>> feed until the filament flow from the nozzle

# Hot to slicing multi-color 3d object

Multi Color 3D printing steps:
Step 1: Load 3D printing model into Cura software.(Fig1)
Step 2: After setting the print parameters, slice to generate the initial gcode code(4C_Niko_Dog_orig.gcode) and preview the model.(Fig2)
Step 3: Open the initial code, add the plug-in, set the plug-in parameters, generate the final print gcode code(4C_Niko_Dog.gcode), and preview the model.(Fig3)
Step 4: print gcode file from SD card. Final physical model.(Fig4)


Fig1 | Fig2 | Fig3 | Fig4

## More detail, please refer to: https://github.com/ZONESTAR3D/Slicing-Guide

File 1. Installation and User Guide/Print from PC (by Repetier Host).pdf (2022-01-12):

# How to print from PC by Repetier-Host

## Version：1.0

## Operation Process

*3D printer can only support gcode files, before placing the 3D model into 3d printer, need to convert the 3D model file (usually they are stl, obj, AMF files) to gcode files, this process is called slicing.

Note: This document only provides a brief description of Repetier-Host. For more details, please search on the web.

## Slicing and print process

## 3D Printing Process

## Repetier-host installation and setting process

## Install the driver (Windows 64-bit)

## 1. Power on printer first!!


## 2. Connect the printer to the PC by USB cable 3. Find communication port

Right click on "Computer" >> "Properties" >> "Device Manager" >> “Other Device“>>”Maple”

Device Manager

Find the directory
of serial driver | Installed driver | Port(COM & LPT)>>Maple (COMxx)
Other Device | Upgrade driver

Find driver

## Please note the port number

## Install Repetier-Host

## Install repetier-host ans slicing engine


## Install Repetier-Host


## Set Parameters


Open Repetier-Host and click on “Printer Settings” in the upper right corner to set the printer parameter.

## Manual Control Menu


Move axis

Hotbed Temperature
Nozzle

Fan Speed

Print Speed

Send gcode to printer

Current position of axis

## Load and Preview gcode file

1. Use Cura software to slice 3D model to gcode file, please refer to Slicing guide for Mixing


## Color Printer V1_1.pdf 2. Load gcode file, preview and then start to print from PC

## User guide for Repetier-host

# https://www.repetier.com/documentation/repetier-host/

## Please refer to the following links for more detailed instructions on how

## to use them


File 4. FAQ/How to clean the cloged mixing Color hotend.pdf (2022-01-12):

# How to clean the clogged mixing-color hotend

Step 1: Heat the hot end (nozzle) to 200 degrees and wait for the temperature to be reached

### Step 2: Remove the fitting and pull out the filament (Figure 1)

Tips 1: If it is difficult to pull out the filaments, you can use the cutting pliers to clamp the filaments and pull out (Figure 2)

Tips 2: If the filaments cannot be pulled out at all, you can use cutting pliers to cut the filaments

### Step 3: Remove the nozzle from the hot end

Note: Please pay attention to prevent burns, it is recommended to wear heat-resistant gloves for operation.

Step 4: Install the hotend-clean-tool on the hot-end (Figure 3), close the channels that are not blocked, and leave only the blocked

channel.

Tips: If the hot end is blocked by filaments and cannot be inserted into the hotend-clean-tool, you can use a lighter to heat the

thin rod of the hotend-clean-tool, and then insert it to the hotend(Figure 4).

Step 5: Manually feed in at least 50cm filaments slowly from the hotend (Figure 5).
Step 6: Clean the filaments in front of the hotend (Figure 6) . If necessary (there are other channels are blocked), you can close the

cleaned channel with a “hotend cleaning tool” before cleaning the next channel.

Step 7: Install the nozzle back.


Figure 1 | Figure 2 | Figure 3 | Figure 4 | Figure 5 | Figure 6

# Why the hotend be clogged

There are many reasons that may cause the hoend to be blocked. Here are some common reasons:

### - Incorrect slicing settings (Figure 7)

Tips: Check the settings in slicing software, to disable “Extruder/Nozzle switching retraction”. For example, set “Nozzle Switch Retraction Distance” to 0 in Cura.

### - Incorrect filament loading

Tips 1: When loading the filament to the hotend, please make sure that the filament enter the heating block of the hot end, it is about 45mm deep into the hot end.

Tips 2: It is recommended to use the “hotend cleaning tool” to close the unused channels of the hotend.

### - Damaged nozzles

Tips: In addition to complete clogging (consumables cannot flow out of the nozzle), the nozzle may also be partially clogged. If you find the filament flowed out from the

nozzle is thinner than normal, the nozzle may be partially clogged. If this happens, you need to use a nozzle cleaning needle to clean the nozzle or replace a new

nozzle directly.

### - The nozzle are too close to the printing platform

Question: If the nozzle is too close to the hot bed when printing the first layer, the filament may not be ejected. If this is maintained for a long time, it may cause the

filament in the hot end to be over-compressed and cause blockage (often blocked at the entrance of hotend).

Solution: Set first layer height = 0.3~0.4mm; heat bed temperature = 70 degrees(PLA); the printing speed 15mm/s (or 50%); Choose “Raft” on “Build Plate Adhesion”

to help filament sticker on the hotbed.

### - Mix different types of filament

Tips 1: Unexpected problems may occur when different types of materials are mixed. It is recommended to use a manual extrusion test before printing large

objects to confirm that the filaments can be extruded normally after mixing.

Tips 2: Before starting to print, extrude some filaments to confirm that the filament can flow out normally.

### - The hot end is overheated

Tips : The overheated hot end may easily cause the hot end to be blocked. Be careful to keep the working temperature of the hot end radiator not exceeding 60

degrees, especially when printing PLA materials. If the hot end is overheated, check the cooling fan and the ambient temperature of the hot end.


### Figure 7

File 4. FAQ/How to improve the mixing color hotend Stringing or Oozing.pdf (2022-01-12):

# How to improve the Mixing Color


# hotend Stringing/Oozing issue

Step 2: Set Auto-Retract to On , and set the relevant parameters such as Retraction distance and Retraction speed.
Step 1: Load the filaments to all the extruders.
PS1: You can load filaments only two extruders too. The more channels you load filaments, the effect if the better.
PS2: The channel without filaments should be closed with hot end clean tool.

How to improve the M3/M4 hotend stringing or Oozing


Retract mm: 8~10 | Unretr. mm: 0
Retract V: 10~20 | Unretr. mm: 8~15
Hop mm: 0~1 (set to 0 if you have set the Z hop in slicing setting)

You can also add a M209 command in the “start gcode” of slicing software
1.Add a “M209 S1” command on the start code
2.Enable Retraction and set the retraction distance to 8~10mm and retraction speed to 30mm/s

How to improve the Mixing Color hotend stringing or Oozing


### Cura


### Simplify 3D

How to improve the Mixing Color hotend stringing or Oozing

### Repetier-HOST

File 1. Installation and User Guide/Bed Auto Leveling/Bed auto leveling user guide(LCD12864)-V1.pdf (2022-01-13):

1. Make sure the hotbed and nozzle are cool, clean the filament on the nozzle.
2. Turn on the 3d printer.
3. Do Montion>> Bed Leveling>> Auto HOME(Fig1).
4. See Montion>> Bed Leveling>> Bed Leveling: OFF, if it is ON, set to OFF(Fig2).
5. Do Montion>> Bed Leveling>> Level Corners(Fig3).
6. Adjust the screws under the hotend, let the nozzle almost to touch the hotend in the four corners (following the wizard)(Fig4).

## Step 1: Level Corners


Fig1 | Fig2 | Fig3


Fig4
NOTE: If the nozzle or Z ENDSTOP is moved, you need to do this step again.

1. Do Montion>> Bed Leveling>> Auto HOME(Fig1).
2. Do Montion>> Bed Leveling>> Catch Z Offset(Fig2).
3. Wait the catching done, check the Z offset:
Do Montion>> Bed Leveling>> Probe Z Offset(Fig3).

## Step 2: Catch Z offset


Fig1 | Fig2 | Fig3

NOTE: It is recommended that the hot bed be heated to about 60 ° for this test.

## Step 3: Level Bed

1. Do Montion>> Bed Leveling>> Auto HOME(Fig1).
2. Do Montion>> Bed Leveling>> Level Bed(Fig2).
3. Watch the measure value, if all of these values are less than 0, it means the “probe Z offset” is too small. (Fig3)
4. Try to add “probe Z offset” (Fig4) a little and then store settings (Fig5).
5. Do 1 and 2 again. (MUST DO AUTO HOME after changed Probe Z offset)
6. After fine tune, the value should be within -0.3mm~0.3mm, and most of the value should be within - 0.1mm~0.1mm.
7. Wait for the end of the test.Operate Auto Home again, the auto leveling will change from off to on. It indicates that the automatic leveling feature is working(Fig7).


Fig1 | Fig2 | Fig3


Fig5


Fig4


Fig6 | Fig7

## Step 4: Verification

Now you can try to print a test file to verfiy the bed auto leveling result
1. Copy level_test_310.gcode to SD card.
2. Print it from SD card.

### 3. When printing started, double click (click twice in one second) the knob to

open Probe Z offset menu (fig1)

### 4. Rotate the knob and watch the nozzle, let the nozzle is higher than the

hotbed about 0.3mm (fig2).

### 5. Do on the MENU>>Configuration>>Store settings (fig3)


Fig1 | Fig3

Fig2


Print result

Auto leveling feature will be disable automatically when the printer reset, you can turn it on manually or let it do automatically every time when printing from SD card.
- Appling it by manually:
1. Motion>> Bed Leveling>> Level Bed >>Auto Home
2. Motion>> Bed Leveling>> Level Bed >>bed leveling: OFF →Change to ON ATTENTION: After do these 2 steps, the printer will apply the hotbed auto leveling correction by using the stored parameters in the last time, it may incorrect.
- Leveling the hotbed at each printing from SD card(Recommend):
You can also add a G29 command to the “start gcode” of slicing software, it will level the bed in the star of printing.
@ Cura | @ Repetier-host Cura Engine | @ Simplify3d

## Apply auto leveling feature


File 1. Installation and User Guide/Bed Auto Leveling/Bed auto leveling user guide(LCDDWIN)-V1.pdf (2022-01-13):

# Auto leveling feaure user guide

# (Z8P-Pro)

## Bed Leveling Sensor: PL-08N

## Note: If the hot bed is enough level without auto leveling, don’t use bed auto leveling feature, Bed automatic leveling will slightly reduce the printing

quality and increase the printing time.

1. Make sure the hotbed and nozzle are cool, clean the filament on the nozzle.
2. Turn on the 3d printer.
3. Do Prepare>> Bed Leveling>> Point1~4.

## 4. Adjust the screws under the hotend, let the nozzle almost to touch the hotend

in the four corners.

# Level Corners


## NOTE: If you moved the position the nozzle or Z ENDSTOP, you need to do this

step again.

## After level coners, please try to print ”level_test_310.gcode” from SD card, and

check if the hotbed is enough level.

# Print test file

Press the knob twice within one second to open the babysteps menu, and then rotate the knob to fine tune the distance from nozzle to hotbed.

## NOTICE: if the hot bed is enough level, Don’t need to use bed auto leveling feature. You can ignore the below steps and start to print

## Step 1. Do Control>> Configure>> Auto Leveling(From OFF to ON) to turn on “Auto leveling” menu


# Auto Leveling >>> Catch Z offset

Step 2. Do Prepare>> Bed Leveling>>Catch Z-Offset.

## PS: if the HOME Z OFFSET is over(>=) 2mm, it will remind to remove the glass first. If you doesn’t use a glass bed, please check the settings of

HOME Z OFFSET.

# Auto Leveling >>> Leveling measure

Step 3. Do Prepare>> Bed Leveling>>Auto Leveling.

After measure done, the state of Auto leveling on Leveling menu will change from Unactived to Actived.


1. The measurement result should be between -1.0 to 1.0 mm. If it exceeds, it is recommended that you try to fine tune the printer or improve the flatness of the hotbed, because it may affect the printing quality.
2. If it is found that there is a large deviation in data arrangement between the Left/Right sides or the Front/Back sides, please adjust the bottom screw of the hotbed (when the data is + turn down the hotbed, when the data is - turn up the hotbed).

# Active auto leveling after printer reset


## Step 5. Do Prepare>> Bed Leveling>>Active Autolevel


## Once power off, the bed autolevel feature will auto unactive, you need to turn on it

on LCD menu.

## Step 4. Print the test file again refer to the page 4

# Supplement

probe Z offset; Probe Nozzle

## - What is “Probe Z offset ”and “HOME Z offset”

“probe Z offset”: it means the distace from the nozzle to the the sensing plane while the probe is triggered. “Catch Z Offset” function will get an average of “probe Z offset” automatically. We MUST manual level the bed by using “Point1~ Point4” before doing “Catch Z Offset”, otherwise the printer can’t get “probe Z offset” correctly.

the sensable plane

## - How to correct “Probe Z offset ” and “HOME Z offset”

For various reasons, the settings of “home Z offset” and “probe Z offset” may not be accurate, so you can manually adjust them to be more accurate.
1. When doing > > bed leveling > > auto leveling,
- if most of the obtained data showed in the table are shifted to the Positive, you can decrease the “Probe Z offset” and do "auto leveling" again ,
- if most of the obtained data showed in the table are shifted to the Negative, you can increase the “probe Z offset” and do auto leveling again.
PS: Ignore the datas at the 4 corners, it will be optimized in the firmware.
2. If you find that the nozzle is too close / far away from the printing plane when printing the first layer, you can incease / decrease home Z offset then print it again.

“HOME Z OFFSET”: For PL-08N bed auto leveling sensor, because it only can sensing a metal object, so “the sensing plane” is the surface of aluminum heatbed, but not the glass. We need to tell the printer the distance from the “real printing plane” to “the sensing plane”, that’s why we need to set the “HOME Z OFFST” to 3.5mm for a glass print plane like Z9V5Pro. By the same token, if we use a magnetic hot bed stickers, we must set “HOME Z OFFST” to 0.8mm ~ 1mm.

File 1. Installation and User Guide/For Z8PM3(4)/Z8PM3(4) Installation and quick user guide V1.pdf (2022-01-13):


# Model: Z8PM3(4)

# User Guide

Please put the printer away from the reach of kids.

Must be guided by adults when children are installed or used.

Take care when installation, to avoid electrical shock hazards.

## Please keep well-ventilated condition! May produce toxic gases when

printer working.

## Caution: Hot!

Hotend has high temperature even the printer stop working.

## Caution: Hot!

Hotbed has high temperature even the printer stop working.

Please strictly follow the standard operation when installation.

## Please make sure you have set the AC power select switch to the

correct position before power on.

## The newest documents download link:

## https://github.com/ZONESTAR3D/Z8P

Parts List

No. | Name | Check | No. | Name | Check
1 | Base Module | □ | 8 | Contol Panel | □
2 | Extruders (3 sets for M3 and 4 sets for M4) | □ | 9 | Scews, lead screws fix blocks, ENDSTOPs, Fittings, PTFE Tubes, belt, cable tie, etc. | □
3 | Z-axis Motor Modules (2 sets) | □ | 10 | Filament Roll Bracket | □
4 | Lead screw & Profiles | □ | 11 | USB cable | □
5 | Print head with bracket M3 or M4 hotend | □ | 12 | Tools | □
6 | Z carrier left | □ | 13 | SD card, Card Reader, Gift filament | □
7 | Z carrier right | □ | 14 | Power cord | □

# Parts

2x Z aluminum profiles, there are 4 taping hole on the end There are 2 hole on the bottom side

These two holes on the bottom when install

1x top aluminum profile, there are many hole on the front

1x X Profile, 2020-420mm, There are two big hole on the back

2x lead screws insert into the Z profie (They are put inside the Z aluminum profiles)


20* M4x18

8* M4x25

Z ENDSTOP

X Belt idler

PTFE Tube | X Timing Belt Z lead screw fix blocks

# Install Z axis Parts

2040V profiles; Z ENDSTOPs; About 18mm

NOTE:
There are two hole
on the profile, let the
side with holes on the
bottom.

Install Zmotor module to the Z profiles

Install Z profiles to base

Install Z ENDSTOPs module to the out side of the Z profiles

# Install Z axis Parts

Install Z Carrier | Install lead screws

Through the copper nut; Top profile

Note:
Adjust the eccentric
cloumns let the carrier
hold the rail well and
move smoothly.

Fixed on the Coupling
of Z axis motor

Install Top profile

# Install X axis Parts

## Install X belt idler and X profile

X Profile

Install the X belt idler to the Z right
carrier, move it from right to left

Install the X profile to
the Z carrier

# Install X axis Parts

## Install X profile


## Slide in the hotend from the right to left

## Layout the hotend cable

Keep the same heigth
Before fixed the X profile

## Install print head (hotend assembly)

# Install X belt

## Install the X belt


Move X belt idler to the right
after fixed the belt | 9

Move X belt idler to the left before fix the belt

## Tigthen the X belt

X Timing Belt

Hotend
(the hotend be hide in this picture)

Adjust the eccentric
cloumns, let the X
carrier hold the rail well and move
smoothly

# Install the other parts

## x 3 o r 4


Install the LCD screen on the right/bottom of printer

Z8-M3 is 3 sets and Z8-
M4 is 4 sets

Install the filament roll bracket to the top of the frame

Connect the extrusion feeder with the print head by filament guide (PTFE tube)

NOTE: One of the channels is connected and others closed by hotend clean tool when the machine left factory. If you don't have experience in using 3D printers, start with single color.

Install Extrusion feeders to the top of the frame

M4x18 *6(8)

NOTE: Try to rotate the extruders a little when install to keep a little clearance between the adjusting screw and the indenter.

M4x18 *2

Keeping the lead screws parallel to the Z axis profiles as far as possible will help to obtain better printing quality, please debug them refer to the following steps: Step 1. Loosen all the screws a little that fixed the Z motors and T8 copper nut. Step 2. Synchronous Rotate the couplings to move up the X axis to 1/2 height of the printer. Step 3. Keep the lead screws parallel to the Z profiles, then tighten the screws that fixed the Z motor

| Loosen a little

and T8 copper nuts.
Step 4. Install the Z lead screws fix blocks on the top profile after done.

200mm

Put in

Fixed

Fixed

# Adjust height of Z ENDSTOPs


Step 1: Adjust the 4 hand nuts under the hotbed, let the hotbed is parallel with bottom profile.
Step 2: Manual rotate the couplings on both of the Z axis motors , let the nozzle touched the hotbed.
Step 3: Move up the ENDSTOP, let its RED part touched the pulley of the Z carriers.
Step 4: Tighten the screws to fix the Z ENDSTOPs

1

2

4

3

## Take care when installation, to avoid electrical shock hazards!

## Double check the wiring! WRONG WIRING MAY DAMAGED THE ELECTRONIC DEVICE!

## Set the 110V/220V swicth (on the side of power supply) to correct position according to your city power voltage!

## Put the motor wire to the grooves of profile and cover them by

plastic profile cover, and using cable tie to wrap the free wires.

## Stop working immediately if the motor has abnormal vibration or noise,, otherwise the driver modules may be damaged!

## Make sure the hotend cooling fan is working when the nozzle

temperature is over 60 degree, otherwise check the wiring again.

## DC-IN, HOTBED has lager operating current, please make sure

these wires contact well with the terminal.

# About electronics parts

X MOTOR and X SW; Y MOTOR and Y SW; Z1 MOTOR and Z1 SW; Extrusion feeders; Hotend cooling FAN; Y MOTOR; AC POWER Switch; AC POWER Connector; Control boarc cooling FAN; 110V/220V Switch; Control Panel; HOTBED; USB socket; Extruder cooling FAN; Knob

DC power button

See from left

Filament run out sensor (Optional)

Bed leveling Sensor

NOTE: Y SW can be installed to

the right side too

Z2 MOTOR and Z2 SW

See from right

SD card socket

# Wiring Block


# Layout the wires / cables

Hotbed cable; BOTTOM VIEW; BACK VIEW; HOTEND Cable; X Motor w/ SW cable

X Motor w/ SW cable
HOTEND Cable
ZL Motor w/ SW cable

E1 Motor
E2 Motor cable
E3 Motor cable
FRODs wire
ZR Motor w/ SW cable
E1 Motor w/ SW cable
EXT3 Motor cable

Y Motor w/ SW cable

Put the motor wire
into the groove of
profile, and cover it by
the profile cover

Step 4: Manually move the hotend and hotbed to see if the movement is smooth, otherwise,

## adjust the eccentric nut until the motor moves smoothly. Refer to the installation

procedure.

## Step 3: Move the hotend and hotbed to their respective limit switch positions to check whether the contact is good and there is a clear sound. Otherwise, please check the limit

switch and reassemble it.

## Step 7: Manually rotate the z-axis screw rod to check whether the z-axis limit switch

contacts reliably.

Step 5: Check whether the X and Y-axis drive belt is firmly installed. If it is too loose, please try to tighten it.

## It is very important to check the machine before power on. It can eliminate the trouble brought by some hardware to ensure the smooth printing!

## Step 6: Check whether the screw rod is assembled in place and whether the screw is tightened

Step 1:Please check if the X&Y axis timing pulley are fixed on the shaft of motor, and the couplings are fixed on the shaft of the Z motors.
Step 2:Please check if the lead screws have been fixed on the shaft of coulping.

Wait the LCD screen off; POWER OFF; “Switch Power Off” on LCD Screen; Turn OFF AC Power Switch; Plug in power cord; Turn ON AC Power Switch; Push and hold DC power button; until the LCD shows Logo and release the DC power button; POWER ON; !!ATTENTION!!; MAKE SURE THE AC VOLTAGE SELECT SWITH HAS BEED SET TO THE CORRECT POSITION!!!

## Knob operation: <Clockwise rotation>: Next Item / Value +. <Counterclockwise rotation>:

Previous Item / Value -. <Push>: Enter / Execute.

Status Message; Printed time; Printing progress rate; Extruder Fan ICON; Current position of axis; Feedrate; Current Virsual toolchain; Mix Rate E0:E1:E2; Mixer ICON; Nozzel setting temperature; Nozzle ICON; Current Nozzel temperature; Hotbed setting temperature; Hotbed ICON; Current Hotbed temperature; Current FAN Speed

For details on the LCD menu, please refer to "LCD12864 Menu Description".

VTOOL: In singel color or general multicolor printer, each extrude motor corresponds to one nozzle, then one extrude + one

nozzle constitutes one tool chain; In mixing color extruder, multiple extrude motors correspond to one nozzle. By setting rotation

ratios of extrude motors can form multiple VTOOL(virtual tool chains). About details, please refer to “Operature guide for

Mixing Color Printer”.

Feedrate: Rotate the knob to set print speed when printing from SD card.

Clean nozzle: make sure there aren't any filament at the end of nozzle, if not, remove it by a diagonal pliers.

1

2

3

Choose “Motion>> Auto Home”>>, wait the hotend go to the orig position.

Watch the nozzle and make sure the nozzle is higher than the bed, otherwise tighten the hand nuts under the bed to pull down the hotbed or loosen these nuts to move up the bed.

4

Choose “Motion>> Level Corners”>>, the nozzle will go to the corners, adjust the hand nuts under the hotbed, let the nozzle almost touch the hotbed. In order to get a properly distance, you can put a A4 paper on the hotbed, and when the distanse between the nozzle and hotbed can only insert a paper, it will be perfect.
Choose “next corner”, and adjust again. Repeat this step again and again, until all of the four corner at the same height. 5

## Congratulations! Now you have finished installation and check, you can start to print

your first works. Before printing, you need to level the hotbed first.


Preheat nozzle: Temperature>> Nozzle, set it to about 180 degree (for PLA) or 220 degree(for ABS and PETG filament), then nozzle will be heated. Waiting nozzle temperature reached to setting.

1

2

Press the handle on the extrude feeder and insert filament, until the filament enter to the hotend.

Choose “Motion>> Move axis>>Extruder>>Move 1mm>>extruder: ****mm”, then Clockwise rotate the knob slowly, until you can see the filament is flowed from the nozzle. 3

## NOTE: We strongly recommend that you start with single color. When the product leaves the factory, we have closed some channels with hotend cleaning tools. You can use

that unclosed channel to print your first work.


# Print a test 3D object (Print from SD card)

2


1 Insert the SD card to the SD card socket on the control box.

Choose “Print from Media”>> Choose “Test_gcode\xyz_cube.gcode”, push the knob to start printing.

3

Wait the printer to finish heating and start to print, watch the distance from nozzle to bed, double click the knob of LCD menu, it will call out a “Babystep Z:” menu , rotate the knob to fine tune the distance from nozzle to the bed, let the filament can stick on the hotbed well.

Insert SD card and
start to print from SD
card

Wait the hotbed and
nozzle heating | Wait for printing finish!

Adjust distance
from nozzle to
the bed
Too Far | Too close | Good

# Slicing

## About slicing

Slicing a 3D drawing translates the 3D drawing into a language that a 3D printer can understand and print. The slicing software is a computer software used in the majority of 3D printing processes for the conversion of a 3D object model to specific instructions for the printer. In particular, the conversion from a model in STL(Obj, Amf) format to printer commands in g-code format. This machine can use a variety of slicing software to complete slicing. We will now introduce the most commonly used slicing software: Cura.
NOTE: 1. Slicing software is not a part of this machine. 2. You can download Cura for free from the internet.

## Install slicing software and step up the printer

In order to run the slicing software, you need a PC or laptabe, installed windows/linux/Macos.
Step 1: Download and install Cura to your PC, please search “ultimaker cura” from google.
Step 2: Copy “cura resources.zip” from the SD card and unzip it to your PC.
Step 3: Copy “resources” file to the same directory in cura which you installed.
Step 4: Run cura software, and follow the below steps to choose the printer.


Download
Cura

Download
Slicing Guide
Load stl files | Setup settings

Slicing and
preview

Store to SD
card

## NOTE: For description of slicing, please refer to the documents in the

directory of “slicing”.

## Slicing process

## You can print something to upgrade your printer, we have made some printed part

and store the stl file to the SD card, you can feel free to slicing it and print it out, and then install them to your kit to make the printer better.


cap_af_20v.stl | cap_af_40v.stl

## lcd12864_case_v2.stl

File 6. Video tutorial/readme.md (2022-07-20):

:movie_camera:[Installation Guide](https://youtu.be/YV3dSoo5NOM)
:movie_camera:[Product introduction](https://youtu.be/NqhwHJeaFhI)

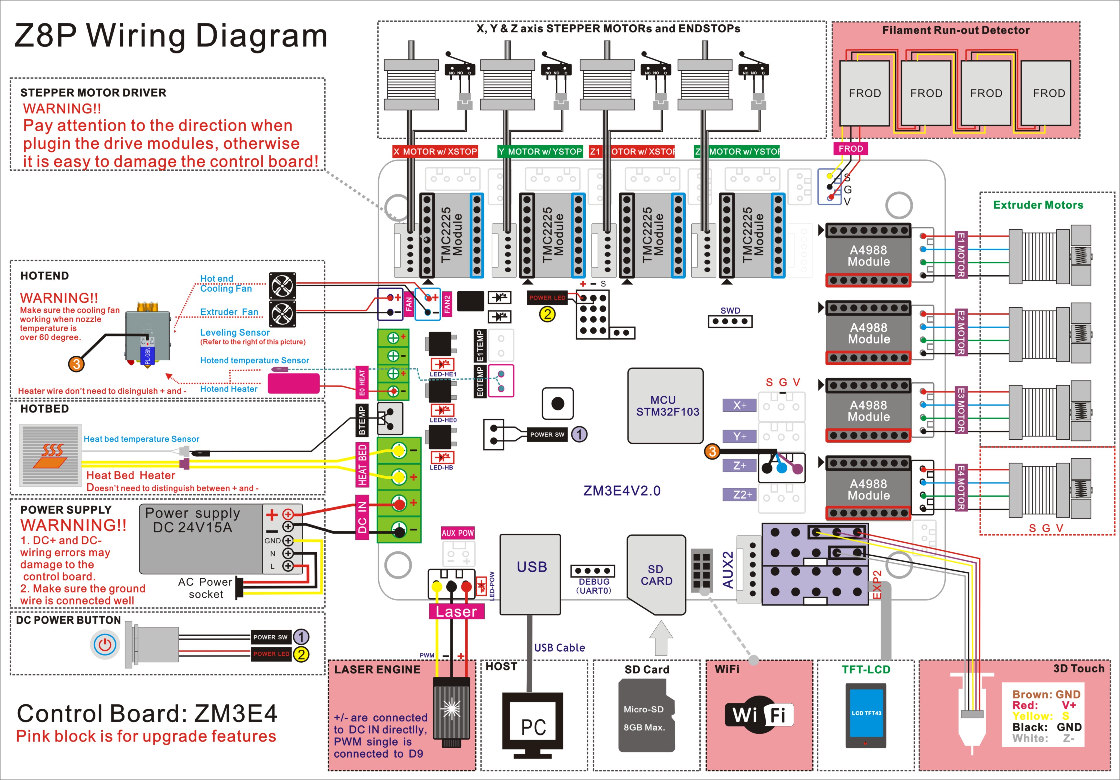
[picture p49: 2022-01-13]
1. Installation and User Guide/Z8P_Pro_Wirig Diagram.jpg

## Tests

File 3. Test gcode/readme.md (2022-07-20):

### [:arrow_down: xyz_cube](xyz_cube.zip)
### [:arrow_down: dog](dog.zip)
### [:arrow_down: Vase](Vase.zip)
### [:arrow_down: PLA temperature correction tower](TempCal_PLA.zip)
### [:arrow_down: Gradient Mixing Vase](GradientMix_Vase.zip)
### [:arrow_down: Random Mixing Vase](RandomMix_Vase.zip)

### How to download
Click the ZIP file and then click the download button.  


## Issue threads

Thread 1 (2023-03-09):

Scaling Problem X Y on Zonestar Z8PM4Pro V2 ?

nicclift, 2023-03-09:
My printer has started trying to get way beyond the limits on the X and Y axes, and when it then starts to print, it does so over the right hand edge of the table, as if it were trying to work on a very much larger table.

I have tried returning to defaults Control/Restore Defaults but no change. I have also tried reinstalling V2.3.2 Firmware. No change

Any suggestions please?

ZONESTAR3D, 2023-03-09:
font{
        line-height: 1.6;
    }
    ul,ol{
        padding-left: 20px;
        list-style-position: inside;
    }

        Hi,
        Your kit should be a Z8PM4Pro-MK2, please use it firmware for MK2.

        https://github.com/ZONESTAR3D/Firmware/tree/master/Z8/Z8P/Z8PM4-MK2

    I attached it too.

                    HallyCTOShenZhen ZONSTAR INNV. Tech. Co., ***@***.***

    ---- Replied Message ----

         From

            ***@***.***>

         Date

        3/9/2023 08:34

         To

            ***@***.***>

         Cc

            ***@***.***>

         Subject

              [ZONESTAR3D/Z8P] Scaling Problem X Y on Zonestar Z8PM4Pro V2 ? (Issue #1)

My printer has started trying to get way beyond the limits on the X and Y axes, and when it then starts to print, it does so over the right hand edge of the table, as if it were trying to work on a very much larger table.
I have tried returning to defaults Control/Restore Defaults but no change. I have also tried reinstalling V2.3.2 Firmware. No change
Any suggestions please?

—Reply to this email directly, view it on GitHub, or unsubscribe.You are receiving this because you are subscribed to this thread.Message ID: ***@***.***>

ZONESTAR3D, 2023-03-09:
Hi,
Your kit should be a Z8PM4Pro-MK2, please use the firmware for MK2.
https://github.com/ZONESTAR3D/Firmware/tree/master/Z8/Z8P/Z8PM4-MK2

nicclift, 2023-03-09:
Thank you! On 9 Mar 2023, at 21:13, ZONESTAR 3D Printer ***@***.***> wrote:

    font{

        line-height: 1.6;

    }

    ul,ol{

        padding-left: 20px;

        list-style-position: inside;

    }

        Hi,
        Your kit should be a Z8PM4Pro-MK2, please use it firmware for MK2.

        https://github.com/ZONESTAR3D/Firmware/tree/master/Z8/Z8P/Z8PM4-MK2

    I attached it too.

                    HallyCTOShenZhen ZONSTAR INNV. Tech. Co., ***@***.***

    ---- Replied Message ----

         From

            ***@***.***>

         Date

        3/9/2023 08:34

         To

            ***@***.***>

         Cc

            ***@***.***>

         Subject

              [ZONESTAR3D/Z8P] Scaling Problem X Y on Zonestar Z8PM4Pro V2 ? (Issue #1)

My printer has started trying to get way beyond the limits on the X and Y axes, and when it then starts to print, it does so over the right hand edge of the table, as if it were trying to work on a very much larger table.
I have tried returning to defaults Control/Restore Defaults but no change. I have also tried reinstalling V2.3.2 Firmware. No change
Any suggestions please?

—Reply to this email directly, view it on GitHub, or unsubscribe.You are receiving this because you are subscribed to this thread.Message ID: ***@***.***>

—Reply to this email directly, view it on GitHub, or unsubscribe.You are receiving this because you authored the thread.Message ID: ***@***.***>

Closed 2023-03-21.

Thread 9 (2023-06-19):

Z-axis Motor Modules do not stop when reach bottom

SLainii, 2023-06-19:
Our new Z8PM4PRO printed one test print, result wasn't good so we started to calibrate the bed. When select "Catch Probe z-offset" machine starts but when Right motor hits to ZSW it clicks but motor won't stop until select something else from LCD. It keep going down and hits to bed and push it downs. Firmware is updated today, and set default. What can be wrong?

Closed 2023-10-17.

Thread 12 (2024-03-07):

Video toturial

ZONESTAR3D, 2024-03-07:
Operation Guide >> Power On/OFF

https://github.com/ZONESTAR3D/Z8P/assets/29502731/2eff055c-82a0-4b11-977d-0ca4e63a27fe

ZONESTAR3D, 2024-03-07:
Operation Guide >> Bed leveling

https://github.com/ZONESTAR3D/Z8P/assets/29502731/3951332c-4483-47b3-b4f5-08acfc49dc3e

ZONESTAR3D, 2024-03-07:
Operation Guide >> Load Filaments

https://github.com/ZONESTAR3D/Z8P/assets/29502731/0661da17-71cf-4c9d-839f-be2c708f6a56

ZONESTAR3D, 2024-03-07:
Operation Guide >> Print From SD Card

https://github.com/ZONESTAR3D/Z8P/assets/29502731/a1d25ecb-89a3-4099-8337-1330adcc3643

ZONESTAR3D, 2024-03-07:
Operation Guide >> Gradient Mixing

https://github.com/ZONESTAR3D/Z8P/assets/29502731/204bb64d-4fe1-47c5-a3e8-98dcdb95c2fe

ZONESTAR3D, 2024-03-07:
Operation Guide >> Random Mixing Color

https://github.com/ZONESTAR3D/Z8P/assets/29502731/b4d3129e-2d2b-4034-9860-ea2db5de49a8
